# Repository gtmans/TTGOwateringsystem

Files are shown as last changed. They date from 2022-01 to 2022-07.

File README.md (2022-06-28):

##### THIS IS WORK IN PROGRESS - NOT FINISHED YET #####

  The goal of this project is to create a wireless sensoring system that controls my watering system (a rainbird raincomputer)
  Whenever one of the soilsensors signals the ground is to dry it triggers a relay that gives input to the raincomputer  

ttgo-water-DHT11

  But first I built a testing system(weatherstation). I started with these 3 modules of prox 12 euro each
  - LilyGO TTGO T-Display V1.1 ESP32 - with 1.14 inch TFT Display
  - LilyGO TTGO T-Higrow ESP32 - BME280 Sensor
  - LilyGO TTGO T-Higrow ESP32 - DHT11 Sensor (its easier to buy 2 of the same Higrows but I got stuck with these)

  I created 2 HTTP servers and one HTTP client inspired by  
  https://RandomNerdTutorials.com/esp32-client-server-wi-fi/
  https://github.com/Xinyuan-LilyGO/TTGO-LoRa-Series 
  https://gist.github.com/jenschr/0fc981415233e0751f22972811b4957f

  Wrote these 2 server programs:
  Program myESP32_server_Higrow_DHT11  Sensorserver1 IP 192.168.2.10 sleeps 70 awake 2 mins white casing
  Program myESP32_server_Higrow_BME280 Sensorserver2 IP 192.168.2.11 sleeps 70 awake 2 mins red casing
  The sensors will be placed outdoors and will be battery based so to make them power efficient 
  I let hem sleep as long as possible (the most I could realise was 70 minutes). So it wakes up every 70 minutes
  and is a server for 2 minutes then goes 2 sleep A 3D printed case can be foud on Thingiverse or Github
  
  Wrote a test program: myESP32_client_T-Display
  
  Next step was to create the base (client) station with humidity threshold setup and a relais
    
  ttgo-water-0 9display
    
  2022-01 
  Built a client based on LilyGO TTGO ESP8266 with 0.91 inch OLED Display
  Started testing:
    
  test1: 2 servers 2 min online every 70 minutes with 800Ma  lipo lasting 21 days!   
  test2: 2 servers 1 min online every 70 minutes with 800Ma  lipo lasting 32 days (2022-20-01 till 2022-21-02)
  test3: 1 servers 1 min online every 70 minutes with 1500Ma lipo lasting 40 days (2022-26-02 till 2022-06-04)
     
  2022-03 new perspective: ESPNOW
  client: LilyGO TTGO ESP8266 - with 0.91 inch OLED Display
  server: LilyGO TTGO T-Higrow ESP32 - DHT11 Sensor 
  Read about ESPNOW and did some tests. Started rewriting the code by using ESPNOW and added a lowpower client using D1 mini & capacitive soil sensor v2.0
  The lipo powered sensors in the garden will wake-up ever 70 minutes and send a message to the client and then check if message is received and goes to deepsleep.   
  If not it will wait 5 seconds and retry 3 times before going to deepsleep. With 800Ma lipo lasting prox 50 days. Sample files in ESPNOW directory
    
  2022-4 D1 mini V3.1 with capacitive soilsensor v2.0 getting 5v from LOLIN batteryshield v1.3 (every 70 minuten in deepsleep) with 800ma lipo is no success: lasts   
  only about 4 days! Going on with ESPNOW and reading things about LORA ...  
   
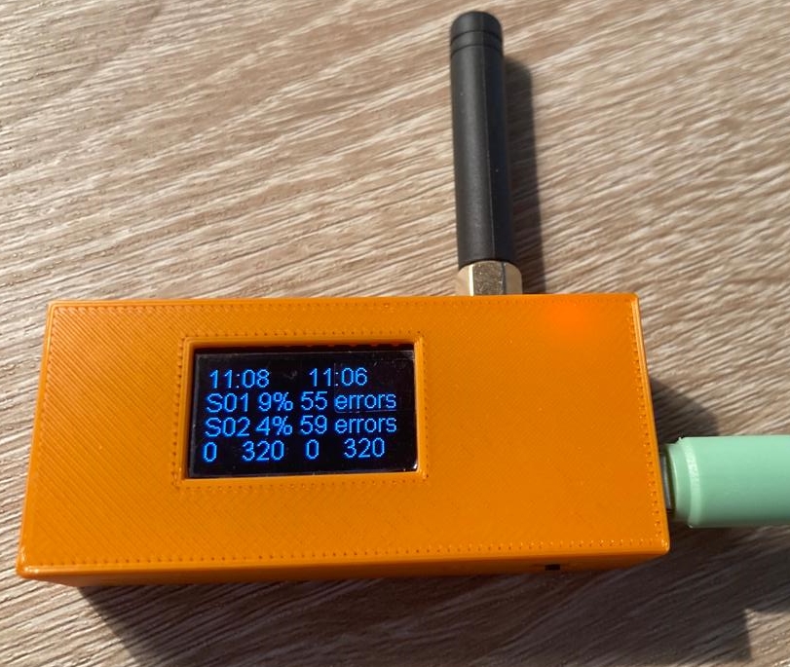
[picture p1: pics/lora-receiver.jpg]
lora-receiver
 
 
  2022-05 Started Lorawan server and client. Is working but the client stops working after some time .... 
  client: LilyGO TTGO T3 LoRa32 868MHz V2.1.6 ESP32
  server: LilyGO TTGO T-Higrow ESP32 - DHT11 Sensor with LilyGO TTGO T-Higrow LoRa Shield - 868MHz

the story continues here:
   more in the readme.md in the lorawan directory: 

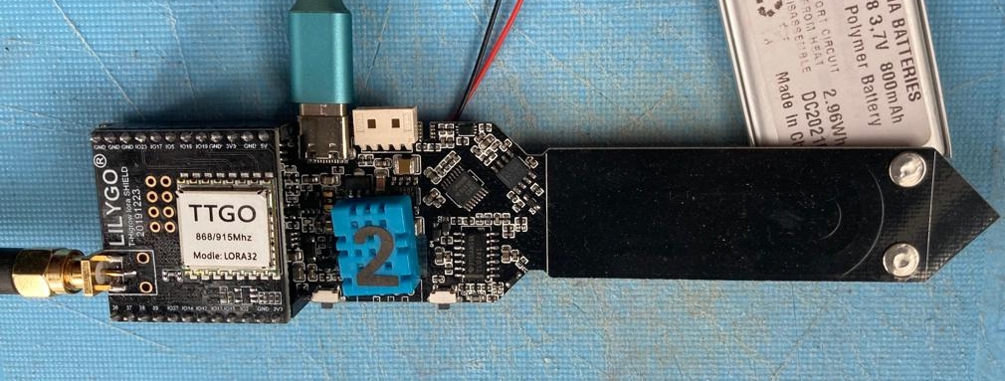
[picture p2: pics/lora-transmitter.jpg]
lora-transmitter


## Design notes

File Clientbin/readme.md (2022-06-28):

Program myESP32_client_T-Display (this program) Just 2 test things I created a sort of monster with these functions:

displays several data gained from internet such as time, weather, and the 2 servers mentioned above

displays screennumber (right above)

displays the status of the 2 sensors ** on/ofline sensr1&1

displays the health of the 2 sensors XX seen within 70 minutes

screen 1 displays internet time

screen 2 displays internet weather (temp, min temp, max temp, humidity, wind speed and direction) and minutes since last reading

screen 3 displays reading of the first sensor DHT11 (temp, humidity, soil humidity) and minutes since last reading

screen 4 displays reading of the first sensor BME280 (temp, humidity, pressure, soil humidity) and minutes since last reading

automated screen roulation

all screens have a landscape mode activated by long press right button

switch screens by short press right button

set clarity by short press left button

check server directly by long press left button

a continous measuring mode

a sleep mode option to save battery. Set go2sleep = true and sleeptime to nr. of milliseconds. After that time readings are stored to eeprom and read from eeprom when starting up

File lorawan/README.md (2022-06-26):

### PLEASE Be aware that this is an ongoing project! ####

The goal of this project is to create a wireless sensoring system that controls my watering system (a rainbird raincomputer) 
Whenever one of the soilsensors signals the ground is to dry it triggers a relay that gives input to the raincomputer

April 2022 I discovered TTGO Lorawan modules which look promising for powerconsumption and range compared to WIFI-ESPNOW.
Inspiration for this project was Timm Bogner's FDRS system:https://github.com/timmbogner/Farm-Data-Relay-System

To test and understand how it works I built a sort of LORANOW construction myself: 
The sensor modules send their readings to the client module which send a confirmation message to the sender. 
If confirmed the sender goes to deepsleep for 70 minutes (max. reliable time) In this test program time is 5 minutes.

lora-transmitter
   
The LoRaReceiver-Higrow.ino is for for (ESP32 Dev Module):LilyGO TTGO T3 LoRa32 868MHz V2.1.6 ESP32 and 
the LoRaSender-Higrow.ino   is for LilyGO TTGO T-Higrow ESP32 - DHT11 Sensor with LilyGO TTGO T-Higrow LoRa Shield - 868MHz
First power measurements of this sender setup is sleep 0,02mA/awake 40mA/lora activity 40-55mA where WIFI uses prox. 125 mA
Both are TEST programs. Finally the receiver will be added a relais and possibly a webserver. 

LORANOW construction.
All information is packet in a text string that is sent using LoRa.beginPacket();LoRa.print();LoRa.endPacket();
Because the text is readable it is simply coded:every character is replaced by another character. 
After sending the sender waits for a confirmation message by using LoRa.receive();LoRa.parsePacket();LoRa.available() and LoRa.read();

2022 may 5 status:
This setup is working perfectly with 2 sensors and 1 receiver exept for the fact that the receiver unit stops working after a few hours (12-36 sender messages)...
No clue at all where it stops - unit seems to hang but display stays on - serial monitor stops after some time (windows)

2022-05-09 Seen something interesting because the serial monitor kept on running longer as usual: The main loop keeps running while there are no more messages received (LoRa.parsePacket() does not get true). Every 60 mins it still does "resetting looptimer" as programmed. So it does not hang but stops receiving ....

2022 06-06 Problems solved. My problems were caused by: 
- testing all modules within centimeters apart from eachother
- with horizontal antennas
- with max radiopower
I made several adjustments and the test programs LoRaReceiver-higrow-16 and LoRaSender-higrow-10.7 (in workingdir) work OK and are in test
I integrated Blynk dashboard (where you can set the threshold and check all important parameters):

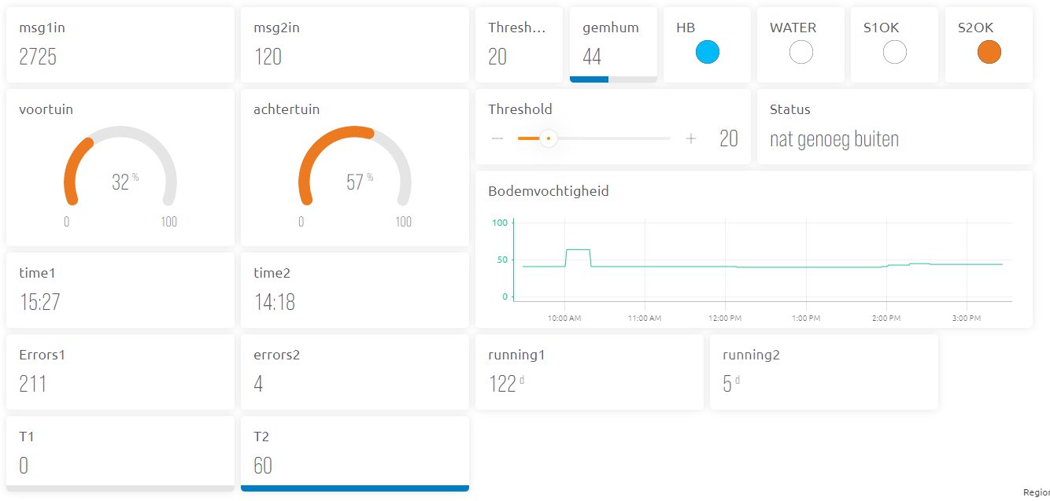
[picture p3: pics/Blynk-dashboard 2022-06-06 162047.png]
blynk_dash


2022-06-13 1st calculation of endurance is 179 days on a 800 mA lipo with sleeptime of 60 minutes (based on a test with 5 minutes sleepingtime)

2022-06-26 System up and running! (pics)

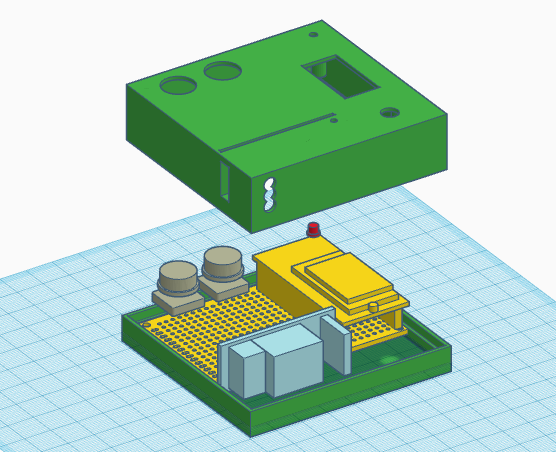
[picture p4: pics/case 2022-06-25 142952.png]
exploded

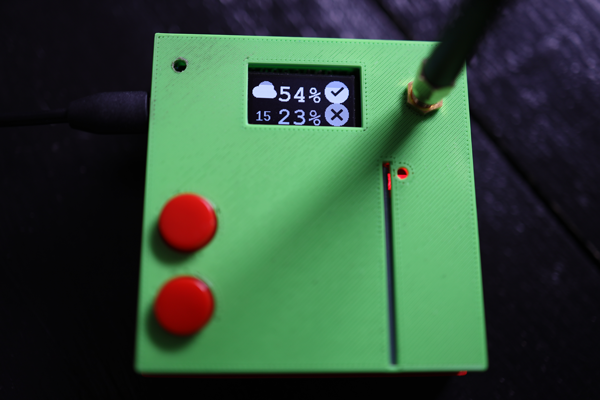
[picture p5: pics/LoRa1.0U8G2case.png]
LoRa1.0U8G2case

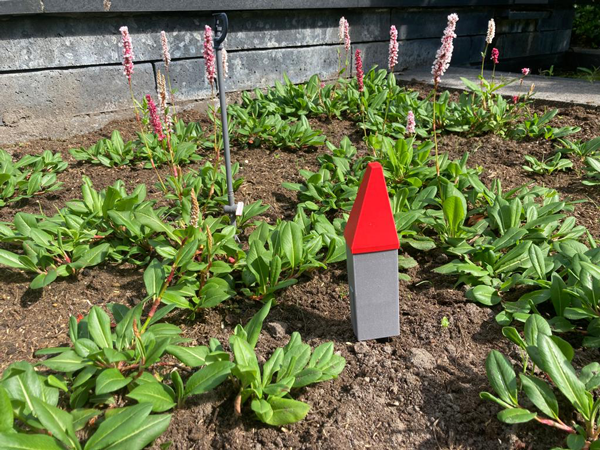
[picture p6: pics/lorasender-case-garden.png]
gardensensor


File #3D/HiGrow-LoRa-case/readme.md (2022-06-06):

All of these .stl files are my design and free to use for everybody

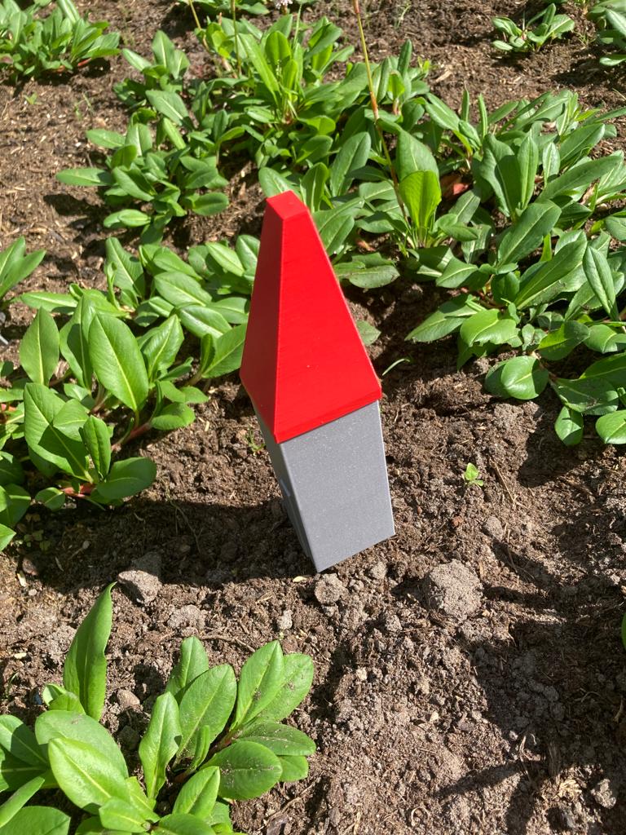
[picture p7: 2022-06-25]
pics/lorasender-case-garden2.jpg

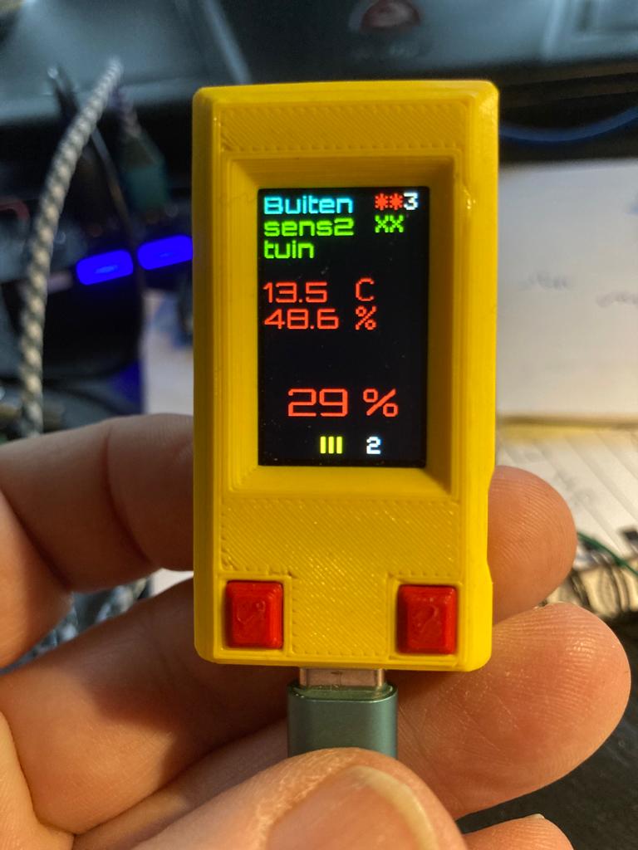
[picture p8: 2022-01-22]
pics/ttgo-water-2.jpg

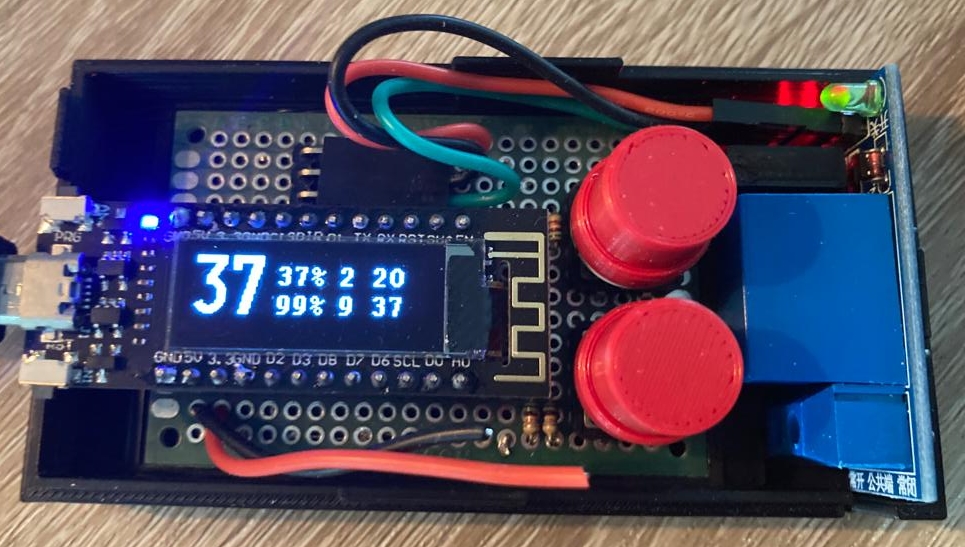
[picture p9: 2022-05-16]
pics/ESPNOW-receiver.jpg

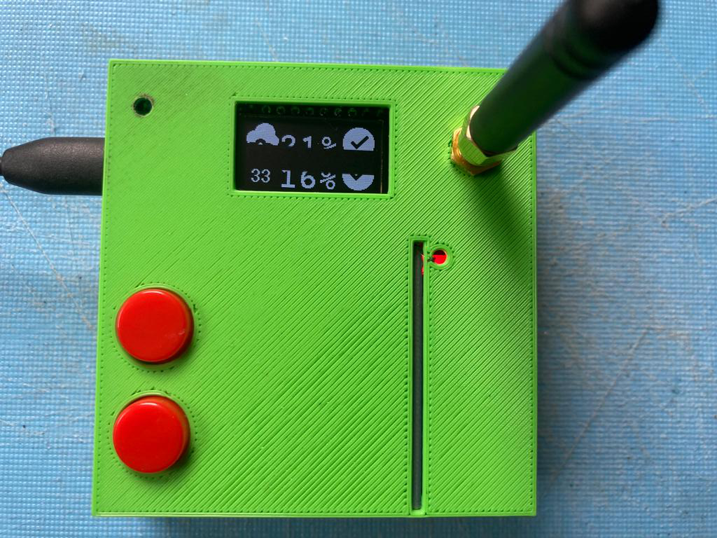
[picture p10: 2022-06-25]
pics/lorareceiver-case.jpg

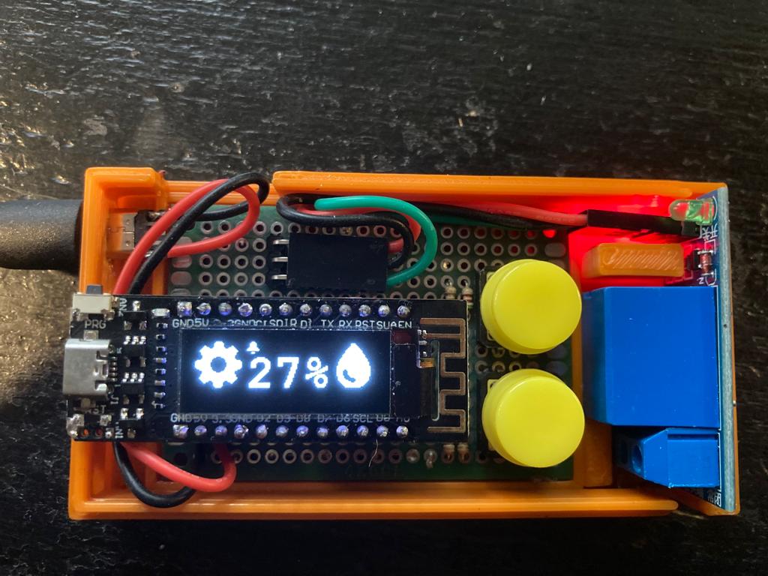
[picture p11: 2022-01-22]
pics/ttgo-water-0.9display.jpg

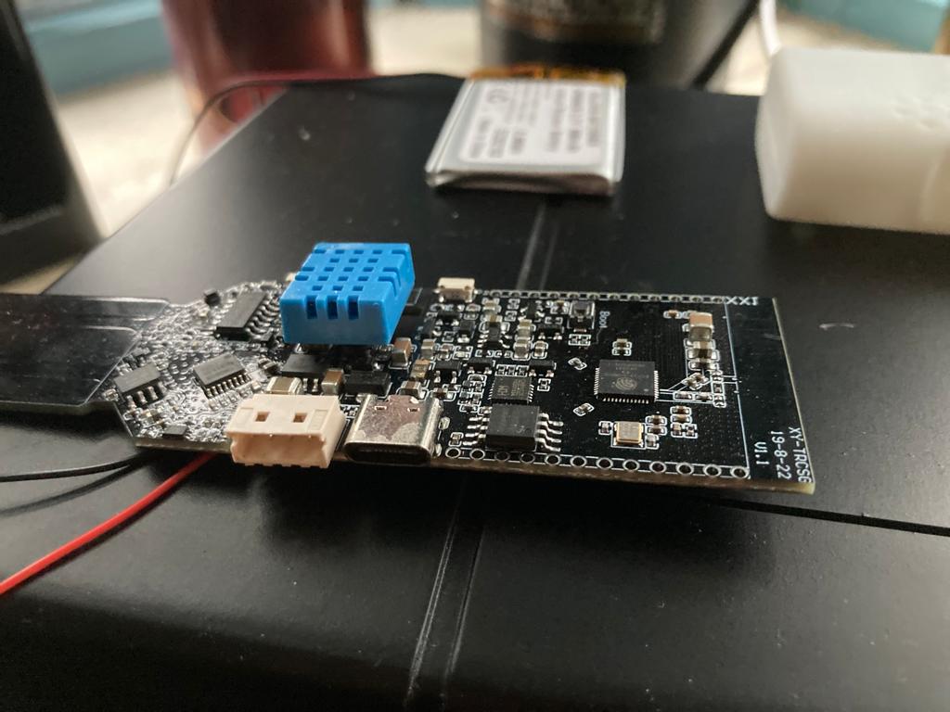
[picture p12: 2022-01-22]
pics/ttgo-water-DHT11.jpg

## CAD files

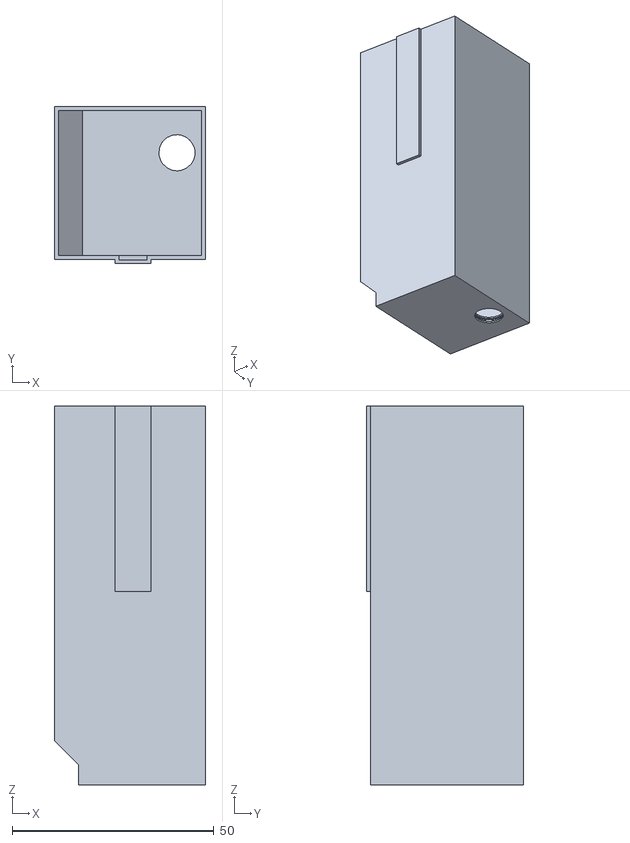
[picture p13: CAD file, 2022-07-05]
#3D/HiGrow-LoRa-case/outside case big for TTGO HIGROW LoRawan.stl
37.5 x 39.0 x 94.0

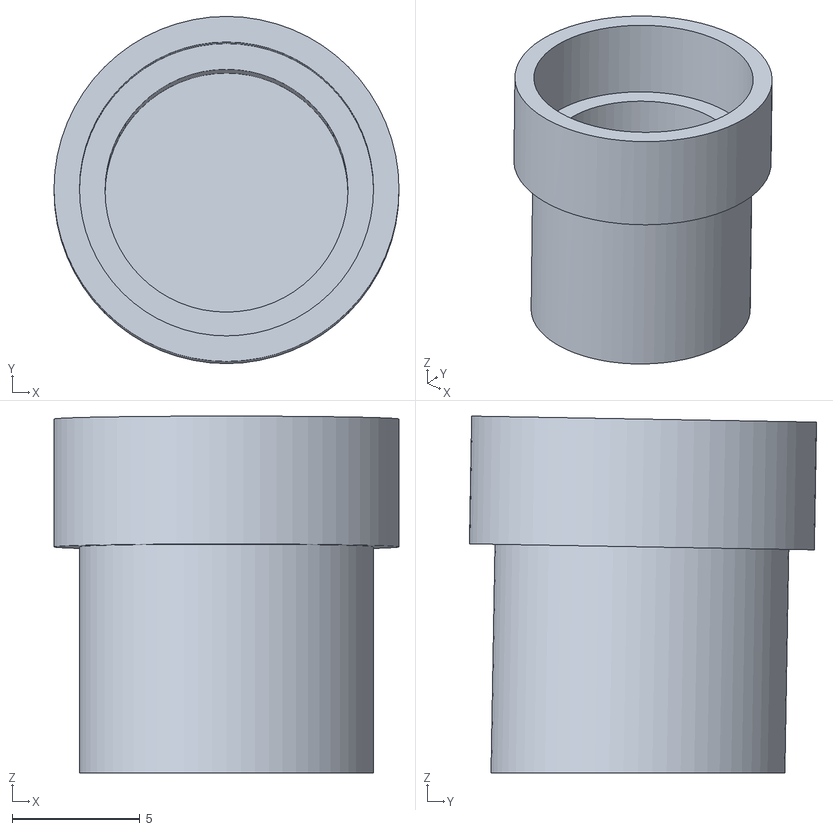
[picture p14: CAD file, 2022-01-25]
Clientbin/CASE ESP-clientv7(knob).stl
13.5 x 13.6 x 14.0

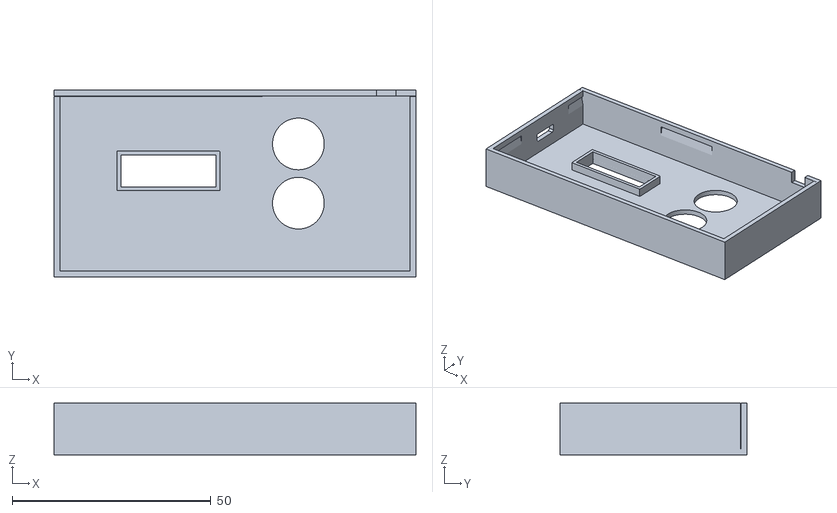
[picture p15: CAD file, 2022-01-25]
Clientbin/CASE ESP-clientv7.stl
91.1 x 47.0 x 13.0

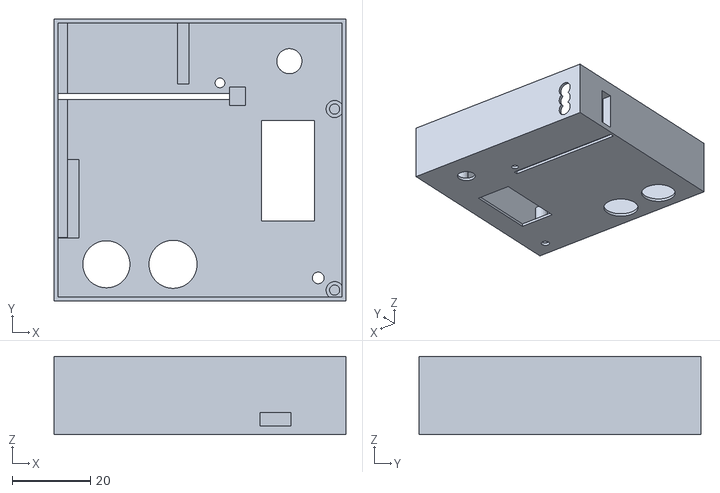
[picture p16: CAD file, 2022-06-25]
#3D/HiGrow-LoRa-case/LilyGOV4.3 TTGO LoRa32 868MHz ESP32 case.stl
74.5 x 72.0 x 20.0

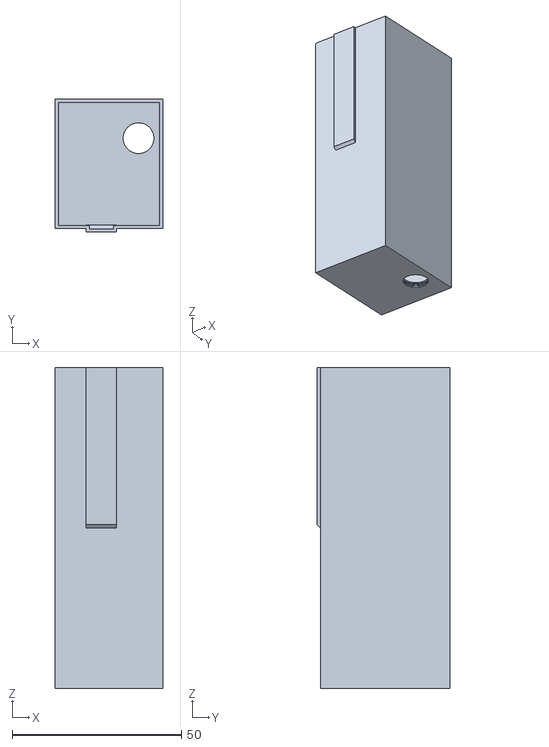
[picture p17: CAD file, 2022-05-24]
#3D/HiGrow-LoRa-case/HiGrow-LoRa-case 1.5 (5.1-101pr).stl
31.8 x 39.4 x 94.9

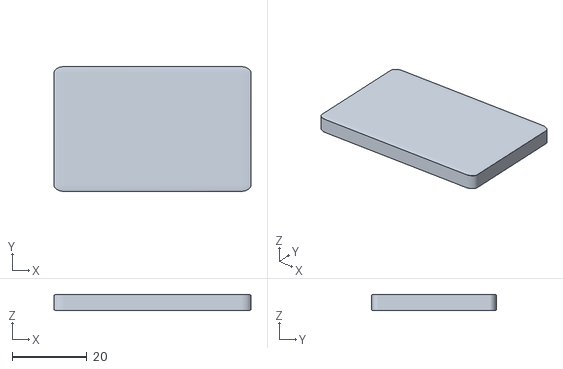
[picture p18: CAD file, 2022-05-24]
#3D/HiGrow-LoRa-case/lipo-800ma-dummy.stl
52.6 x 33.3 x 4.40

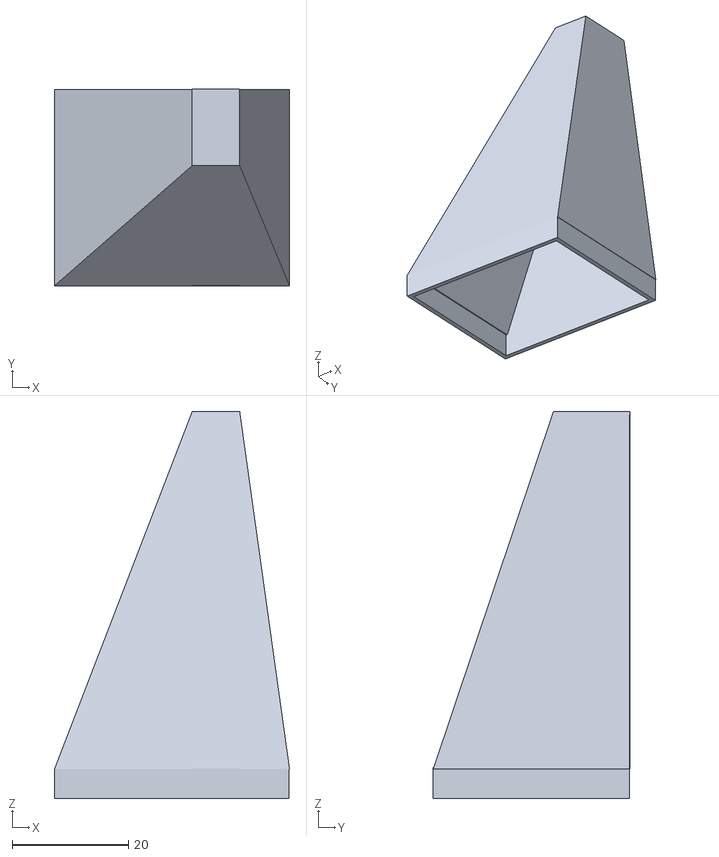
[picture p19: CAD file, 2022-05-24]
#3D/HiGrow-LoRa-case/HiGrow-LoRa-case 1.5 (6-101pr).stl
40.5 x 33.9 x 66.7

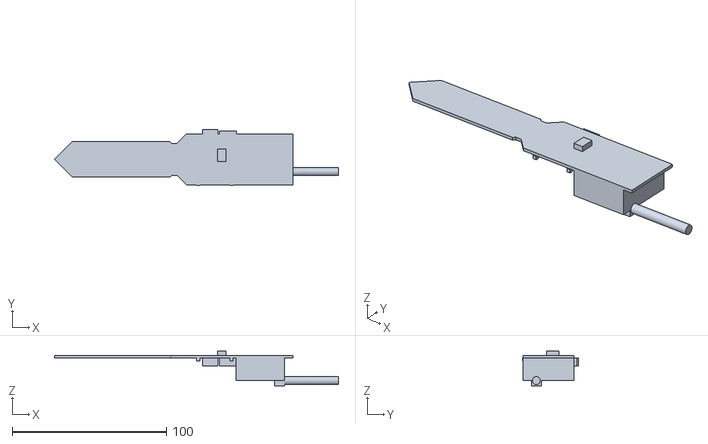
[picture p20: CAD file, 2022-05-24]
#3D/HiGrow-LoRa-case/HiGrow-LoRa-dummy.stl
183.9 x 36.5 x 22.5

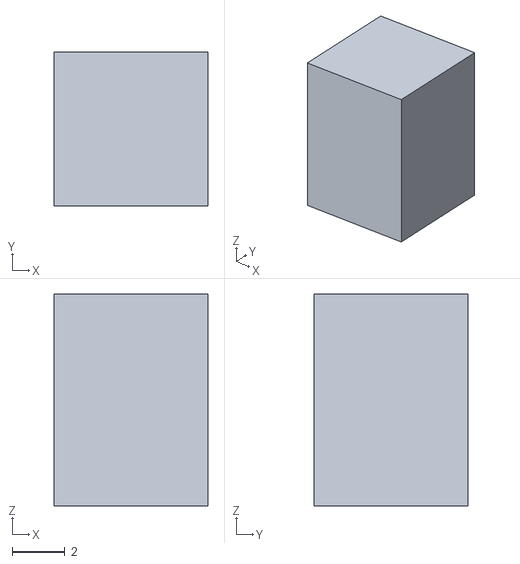
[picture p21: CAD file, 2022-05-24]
#3D/HiGrow-LoRa-case/HiGrow-LoRa-case 1.5 (4).stl
5.80 x 5.80 x 8.00

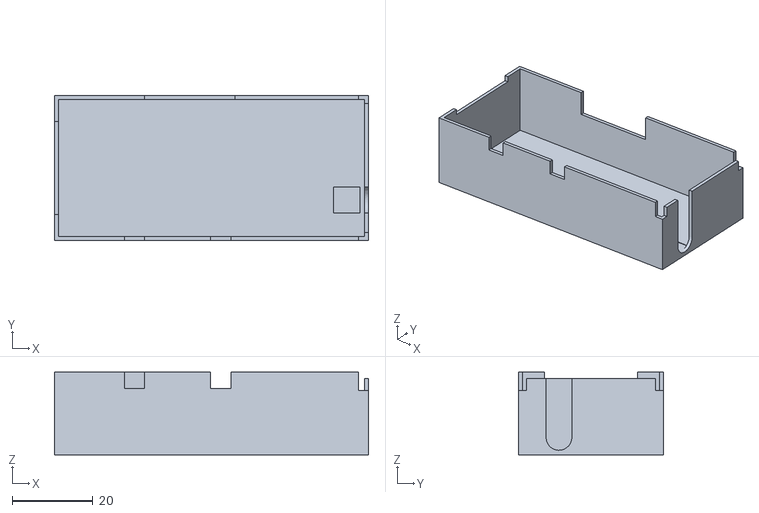
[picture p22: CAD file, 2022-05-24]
#3D/HiGrow-LoRa-case/HiGrow-LoRa-case 1.5 (1).stl
78.0 x 36.0 x 20.5

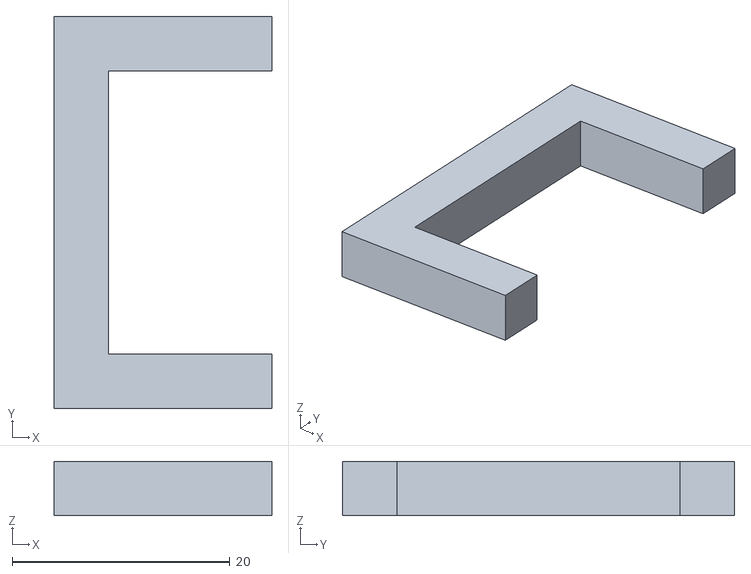
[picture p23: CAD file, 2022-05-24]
#3D/HiGrow-LoRa-case/HiGrow-LoRa-case 1.5 (3).stl
20.0 x 36.0 x 5.00

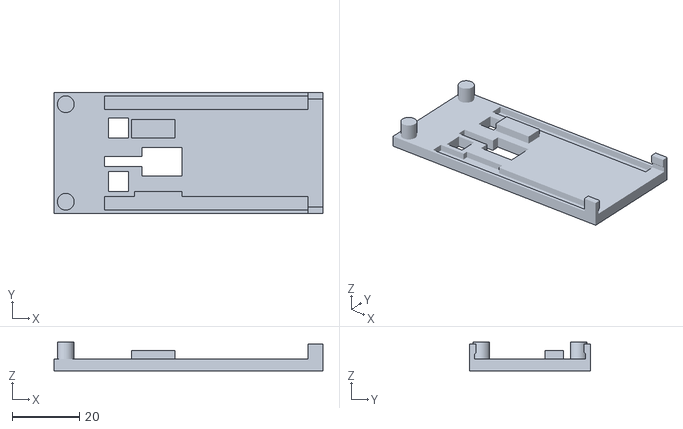
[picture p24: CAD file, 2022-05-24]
#3D/HiGrow-LoRa-case/HiGrow-LoRa-case 1.5 (2).stl
80.0 x 36.0 x 8.50

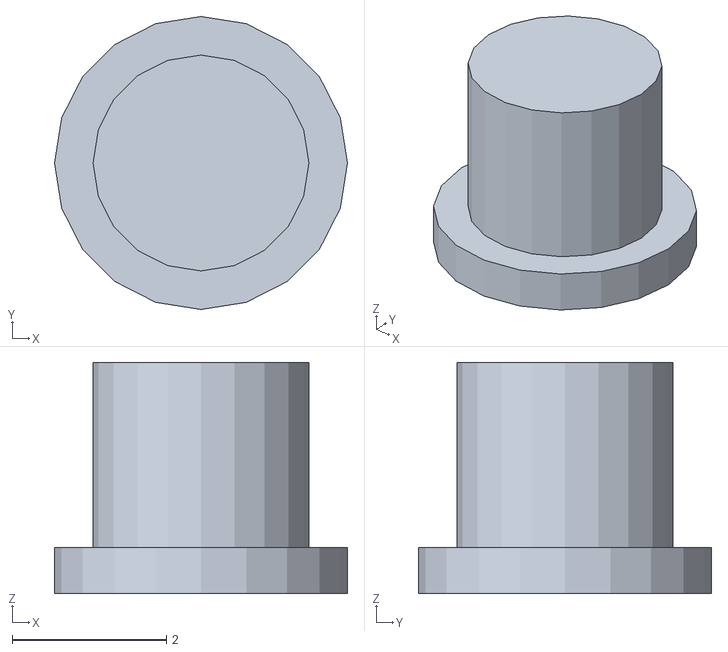
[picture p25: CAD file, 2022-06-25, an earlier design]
#3D/HiGrow-LoRa-case/LilyGOV4.3 TTGO LoRa32 868MHz ESP32 case (2).stl
3.80 x 3.80 x 3.00

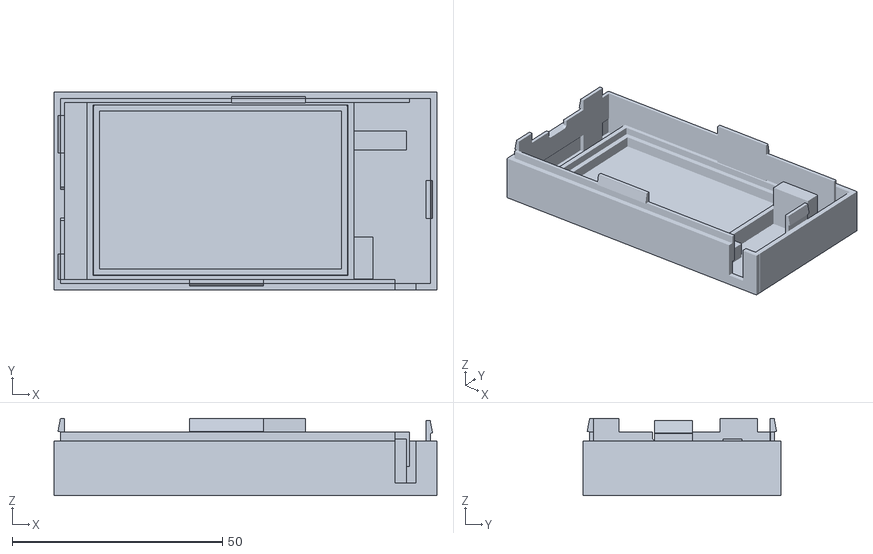
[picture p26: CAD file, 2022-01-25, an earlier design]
Clientbin/CASE ESP-clientv7 (1).stl
91.1 x 47.0 x 18.4

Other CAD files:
#3D/HiGrow-LoRa-case/LilyGOV4.3 TTGO LoRa32 868MHz ESP32 case (1).stl

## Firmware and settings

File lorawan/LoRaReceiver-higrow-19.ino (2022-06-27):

/* \Arduino\LORAWAN\TTGO-LoRa-Series-master\LoRaReceiver\LoRaReceiver-higrow-19 to use with
 * \Arduino\LORAWAN\TTGO-LoRa-Series-master\LoRaSender\LoRaSender-higrow-10.9
 * for (ESP32 Dev Module):LilyGO TTGO T3 LoRa32 868MHz V2.1.6 ESP32
 * reads text records from lorasenders higrow
 */
#define OLDLORA    1            // SET! when using 1.0 board io. 2.14
#define SND_MSG    1            // SET! confirmation message
#define USE_U8G2   1            // SET! use graphic signs io. text
#define RST_ESP    1            // SET! restart ESP every 60 min to avoid hanging(set value interval below)
#define CHK_RSSI   1            // SET! display last RSSI and SNR
#define CHK_HEAP   1            // SET! check memory heap
#define USE_WIFI   1            // SET! use WIFI to get timestamp
#define USE_EEPR   1            // SET! store la  st read values in eeprom
#define USE_BLYNK  1            // SET! use of Blynk dashboard
#define USE_RELAIS 1            // SET! version with relais and buttons
#define SND_MSGX   0            // SET! extra confirmation message
#define DEBUG      0            // SET! dump incoming string to screen or just their values
#define CHK_XTRA   0            // SET! check first byte of message is yours
#define CHK_LORA   0            // SET! check if lora.receive still active
#define USE_INSIDE 0            // SET! reduce radiosignal when testing
#define USE_SYNCW  0            // SET! use syncword to avoid stay messages (set in sender sketch too)
#define MIDNIGHT   0            // SET! restart ESP at midnight
#define NrSensors  2            // SET!
#define BUT_IN     0            // onboard button to turn screen off
#define LED_IN     2            // onboard led indicates water

#if USE_RELAIS                  // note! pinout of 1.0 and 2.0 board is different but both have these pins
  #define         relayPin  14
  #define         lbutton   12
  #define         rbutton   13 
  bool            buttons;       // are there buttons attached to set threshold? 
  bool            water   =false; 
  bool            oldwater=false; 
#endif

#if   USE_BLYNK
/*
 * https://blynk.cloud/dashboard  create a template with:
 * 
 * Id Name          Pin Datatype  Units min max def
 * 1  time1s        V0  String  
 * 2  time1s        V1  String  
 * 3  Thresholdi    V2  Integer         0   100   0
 * 4  Statuss       V3  String
 * 5  FrogardenperciV4  Integer    %    0   100   0
 * 6  BckgardenperciV5  Integer    %    0   100   0
 * 7  msg1ins1      V6  String
 * 8  msg1ins2      V7  String
 * 9  avghumi       V8  Integer         0   100   0
 * 10 wateri        V9  Integer         0   1     0
 * 11 errors1i      V10 Integer         0   32767 0
 * 12 errors2i      V11 Integer         0   32767 0
 * 13 running1i     V12 Integer    d    0   999   0
 * 14 running2i     V13 Integer    d    0   999   0
 * 15 S1OK          V14 Integer         0   1     0
 * 16 S2OK          V15 Integer         0   1     0
 * 17 Heartbeat     V16 Integer         0   1     0
 * 18 Since1i       V17 Integer         0   999   0
 * 19 Since2i       V18 Integer         0   999   0
 * 20 Thresholdseti V19 Integer         0   100   15
 * 21 RSSI1s        V20 Stringr                    
 * 22 RSSI2s        V21 Stringr                    
 * 23 Switch        V22 Integer         0   1    
 */ 
  #define BLYNK_PRINT Serial
  #if OLDLORA     // I have 2 different boards they use different template                             
    #define BLYNK_TEMPLATE_ID "TMPL878asd6f"                      // SET!
    #define BLYNK_DEVICE_NAME "mygarden"                          // SET!
    #define BLYNK_AUTH_TOKEN  "TKM9cdkslfji43566j6836j4654Wyzp8"  // SET!
  #else
    #define BLYNK_TEMPLATE_ID "TMPLklfdsj6Y"
    #define BLYNK_DEVICE_NAME "myDash"
    #define BLYNK_AUTH_TOKEN  "igpogiafgmkJHJYqwetHupoiflcdxkmU"
  #endif
  #include <BlynkSimpleEsp32.h>
  bool  flip;                     // for heartbeat led blynk
  char  auth[] = BLYNK_AUTH_TOKEN;
  int       TsinceS1;             // minutes gone since last reading sensor 1
  int       TsinceS2;             // minutes gone since last reading sensor 2
  BlynkTimer timer;
  WidgetLED led1(V9);
  WidgetLED led2(V14);
  WidgetLED led3(V15);
  WidgetLED led4(V16);
  #if !defined USE_WIFI
    #define    USE_WIFI
  #endif
#endif

#if  RST_ESP
//  long interval     = 3600000; // SET! interval  60 minutes to restart ESP every 60 min to avoid hanging
  long interval       = 7200000; // SET! interval 120 minutes to restart ESP every 60 min to avoid hanging
  long previousMillis =  millis  ();
#endif

#if  CHK_LORA
  long interval2       =  450000; // SET! interval 7.5 minutes to check lora(band) to avoid hanging
  long previousMillis2 =  millis  ();
#endif

#if  CHK_RSSI
  int snr;
  int rsi;
  int snrv [NrSensors]={0,0};
  int rsiv [NrSensors]={0,0};
#endif

#if  CHK_HEAP
  #define HEAP_DIF  10000        // SET! reset when memory loss > HEAP_DIF
#endif

#if  OLDLORA
  #include "lora1.0_board_def.h" // for 1.0  board with seperate antenna
#else  
  #include "lora2.0_board_def.h" // for 2.14 board with onboard  antenna
#endif

#if  USE_WIFI
  #include <ArduinoJson.h>
  #include <NTPClient.h>
  #include <WiFi.h>
  #include <WiFiUdp.h>
  #include <WiFiClient.h>
  #include "my_secrets.h"                       //or use 2 lines below
  //#define WIFI_SSID       "yourWIFISSID"      // ssid
  //#define WIFI_PASSWORD   "yourWIFIPassword"  // password
  //RTC
  StaticJsonDocument<1000> doc;
  WiFiUDP   ntpUDP;                // Define NTP Client to get time
  NTPClient timeClient(ntpUDP);    // Variables to save date and time
#endif

#include <SPI.h>
#include <LoRa.h>

#if USE_EEPR
  #include "EEPROM.h"
  String EepSave [NrSensors]={"11:11MYDATA01113500200020","11:11MYDATA01113500200020"};//25 long
#endif

String Sensors [NrSensors]={"S99 99% 999 errors.","S99 99% 999 errors."}; //20 long
String SensMes [NrSensors]={"?????","?????"};   //5 long
String SensTim [NrSensors]={"wait!","wait!"};   //5 long
int    NrMsgs  [NrSensors]={0,0};
int    Humi    [NrSensors]={33,33};
int    Temp    [NrSensors]={0,0};//temp or errorcounter
int    count    = 0;              // total nr of correct received packages
int    expLEN   = 20;             // SET! length of "MYDATA01102500100000"
int    flop     = 0;              // for heartbeat oled
int    mytimer  = 0;
String ID       = "MYDATA";       // SET! your chosen identifier
String expID    = ID;         
// choose your own coding/decoding strings but use same strings as in sender program
String normal   = "ABCDEFGHIJKLMNOPQRSTUVWXYZ1234567890+-";//SET! decode
String coded    = "1234567890abcdefghijklmnopqrstuvwxyz-+";//SET! code (pa A becomes 1)
String msgin    = "MYDATA01102509900000";
String msgout   = msgin;
String recv     = msgin;
String subst    = "X";
String LoRaStat = "*";
String myMessage=msgin;
String sentence=msgin;
String SN="99";                   // sensor number
String DN="9";                    // destination number
String TT="999";                  // temp reading(3)
String HH=TT;                     // hum reading (3)
String MN="99999";                // messagenumber (5)
int    T;                         // temp   reading  as integer
int    H;                         // hum    reading  as integer
int    S;                         // sensor  number as integer
int    M;                         // message number as integer
int    Threshold  = 15;
int    oldThreshold  = Threshold;
long   freememstart;  
String formattedDate="2018-05-28T16:12:34Z";
String TimeStamp="99:99";
bool   LCDon=true;
String msg;
String STHours;
String STMinutes;
int    TMinutes;
int    PrevMins[NrSensors]={0,0};
int    gemhum=15;

#if USE_U8G2
  #include <U8g2lib.h>
  // fontlists at https://github.com/olikraus/u8g2/wiki/fntlistall
  #if OLDLORA 
      U8G2_SSD1306_128X64_NONAME_F_SW_I2C u8g2(U8G2_R0, OLED_SCL, OLED_SDA , OLED_RST);
  #else
      U8G2_SSD1306_128X64_NONAME_F_SW_I2C u8g2(U8G2_R0, OLED_SCL, OLED_SDA , U8X8_PIN_NONE);
  #endif  
#else
  OLED_CLASS_OBJ display(OLED_ADDRESS, OLED_SDA, OLED_SCL);
#endif

#if  USE_BLYNK
  // This function will be called every time Slider Widget
  // in Blynk app writes values to the Virtual Pin V19
  BLYNK_WRITE(V19)
  {
  int pinValue = param.asInt(); // assigning incoming value from pin V19 to a variable
  // process received value
  Threshold = pinValue;
  Blynk.virtualWrite  (V2, Threshold);
  //Blynk.virtualWrite  (V19,Threshold);
  Serial.println    ("*blynk slider");
  }

  BLYNK_WRITE(V22)// reset switch
  {
  int pinValue = param.asInt(); // assigning incoming value from pin V19 to a variable
  // process received value
  Serial.println    ("*blynk switch");
  resettime();
  }
  
  // This function is called every time the device is connected to the Blynk.Cloud
  BLYNK_CONNECTED()
  {
      Blynk.virtualWrite  (V3 ,"Verbonden met Blynk");
      Blynk.virtualWrite  (V2, Threshold);
      Serial.println      ("Blynk_Connect");
      led1.off  ();
      led2.off  ();
      led3.off  ();
      led4.on   ();
  }
  // This function sends ESP32 uptime every 10 seconds (see timer.setInterval) to some virtual Pins
  void myTimerEvent()
  {   
//    String msg;
    gemhum =(Humi[0]+ Humi[1])/2;
    if (gemhum<Threshold){water=true;led1.on();msg="ga sproeien!"; 
    } else {water=false;led1.off();msg="nat genoeg!";}
    digitalWrite(LED_IN,water);
    if (flip){led4.on();}else{led4.off();}flip=!flip; 
    Blynk.virtualWrite  (V3,  msg);
    Blynk.virtualWrite  (V8,  gemhum);
    Blynk.virtualWrite  (V2,  Threshold);
    Blynk.virtualWrite  (V5,  Humi   [1]);
    Blynk.virtualWrite  (V4,  Humi   [0]);
  }
#endif
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
void loop(){

  unsigned long currentMillis = millis(); 
  flop++;                     //display heartbeat on oled
  if (flop>50000){            // 5   secs
    flop=0;
    if (LoRaStat=="+"){LoRaStat="x";} else {LoRaStat="+";}
    displayOled();

    #if  USE_BLYNK
    mytimer++;
    if (mytimer==10){          // prox 1 min set leds and blynk values
        mytimer=0;
        SetLeds();
      }      
    #endif 
  }

  #if USE_RELAIS  
    if (Threshold!=oldThreshold){displayThresh();ThresholdToEeprom();oldThreshold=Threshold;}
    if (water && !oldwater){        // water has become true turn on relay
      digitalWrite(relayPin,HIGH);
      oldwater=true;
      Serial.print       ("water has become true  turn on relay ");
      Serial.print       (gemhum); 
      Serial.print       ("/");
      Serial.println     (Threshold);
    }        
    if (!water && oldwater){        // water has become false turn off relay
      digitalWrite(relayPin,LOW);
      oldwater=false;    
      Serial.print       ("water has become false turn off relay ");
      Serial.print       (gemhum); 
      Serial.print       ("/");
      Serial.println     (Threshold);
    }   
  #endif
  
  #if  USE_BLYNK
    Blynk.run();
    timer.run();
  #endif
  
  #if  CHK_LORA
    if   (currentMillis - previousMillis2 > interval2) {
        if (!LoRa.begin(BAND)){
          Serial.println      ("Checking LoRa failed! Restarting ...");
          delay               (500);      
          ESP.restart         ();    
        }    
        Serial.println        ("LoRa OK, resetting looptimer");
        LoRaStat        =     "+";
        previousMillis2 =     currentMillis;
    }
  #endif

  #if  RST_ESP
    if   (currentMillis - previousMillis > interval) { 
      Serial.println        ("restarting ESP after interval.");
      delay                 (500);      
      ESP.restart           ();
    }
  #endif

  int packetSize = LoRa.parsePacket();
  if (packetSize) {  
      recv = "";
//    while (LoRa.available()) {recv += (char)LoRa.read();} ## replace
      while (LoRa.available()) {recv  = LoRa.readString();}

      #if  CHK_RSSI
        snr= LoRa.packetSnr ();
        rsi= LoRa.packetRssi();
        Serial.print        ("RSSI/SNR:");      
        Serial.print        (rsi); 
        Serial.print        ("/"); 
        Serial.println      (snr); 
      #endif
      
      int lenIN   =       recv.length();      // length of "MYDATA01100200100047"
      Serial.print        ("received package long ");      
      Serial.println      (lenIN); 

      if                  (lenIN==expLEN){
        #if CHK_XTRA
          //XTRA CHK 2 PREVENT HANGING ESP
          String CHK = recv.substring(0,1); //"c"
          int p = coded.indexOf     (CHK);  //12
          subst = normal.substring  (p,p+1);//"M"
          #if DEBUG
              Serial.print      (CHK);   
              Serial.print      (p);   
              Serial.println    (subst);           
          #endif
          if (expID.substring(0,1)!=subst){ID="X";} // extra check: 1st character of message is as expected
        #endif 
                 
        if (ID!="X"){
          codit      (recv,false);        // now convert coded msgin to msgout
          recv    =   msgout;
          ID      =   recv.substring(0,6);// "MYDATA"          
          count++;
        }
          
        if (ID==expID){
          //"MYDATA01102509900000"
          breakdown(recv);                // get vars out of message

          // now send conformation message
          // identifier send to sender 0? from receiver 1 = me received OK
          // myMessage ="MYDATA0?1OK";
        
          myMessage =expID;               //"MYDATA"
          myMessage+=SN;                  // 01 or 02
          myMessage+=DN;                  // former destination = 1 = me
          myMessage+="OK";                // "MYDATA011OK"         
          codit(myMessage,true);          // convert msgin to coded msgout
          myMessage=msgout;

          #if SND_MSG
            Serial.print        ("sending  :");   
            Serial.println      (myMessage);  
            LoRa.beginPacket    ();
            LoRa.print          (myMessage);
            LoRa.endPacket      ();
            //2testlater        LoRa.endPacket(true); // true = async / non-blocking mode
            //https://www.rfwireless-world.com/Terminology/What-is-difference-between-Implicit-header-and-Explicit-header-in-LoRaWAN-packet.html
          #else
            Serial.println      ("Not sending confirmation message.");
          #endif

          #if USE_WIFI
            formattedDate   =   timeClient.getFormattedDate();
            int pos         =   formattedDate.indexOf("T");
            TimeStamp       =   formattedDate.substring(pos+1, formattedDate.length()-1-3);
          #else
            TimeStamp       =   "99:99";
            delay (250);
          #endif

          S = SN.toInt  ();      
          ParseReadings (S,true);// store data in arrays and update counter                      
          LoRaStat  =   "R";
          
          #if DEBUG
            displayDebug();
          #else
            displayOled();          
          #endif

          #if SND_MSGX        //SEND AGAIN 2 BE SURE        
            delay             (1000); 
            Serial.print      ("sending  :");   
            Serial.println    (myMessage);  
            LoRa.beginPacket  ();
            LoRa.print        (myMessage);
            LoRa.endPacket    ();
          #else
            delay (50);
          #endif

          #if DEBUG
            displayDebug();
          #else
            displayOled();          
          #endif

          #if USE_EEPR
            WriteToEeprom       ();         // update eeprom values for reset or restart
          #endif

          #if  USE_BLYNK
              GetMinutes       (TimeStamp);
              PrevMins [S-1] = TMinutes;             
              M=SensMes[S-1].toInt();

              if (S==1){
                led2.off();
                Blynk.virtualWrite(V0 ,SensTim[0]);
                Blynk.virtualWrite(V4 ,Humi   [0]);
                Blynk.virtualWrite(V6 ,SensMes[0]);
                Blynk.virtualWrite(V10,Temp   [0]);
                Blynk.virtualWrite(V12,String(M/24));                                 //days  running 24hpd
                Blynk.virtualWrite(V20,String(snrv[0])+"/"+String(rsiv[0]));          //signal strength
              } else {
                led3.off();
                Blynk.virtualWrite(V1 ,SensTim[1]);
                Blynk.virtualWrite(V5 ,Humi   [1]);
                Blynk.virtualWrite(V7 ,SensMes[1]);
                Blynk.virtualWrite(V11,Temp   [1]);
                Blynk.virtualWrite(V13,String(M/24));                                 //days  running 24hpd
                Blynk.virtualWrite(V21,String(snrv[1])+"/"+String(rsiv[1]));          //signal strength
              }
          #endif

          #if SND_MSG
            delay(1000);LoRa.receive();                                               // after sending start receiving again
          #else
            LoRaStat="I";
            displayOled();                                                            // end of some packet same length
          #endif 
         
      } else { // not expected ID
          Serial.println  ("Package is not mine ... wrong ID ignoring package");         
      }
    } // end of len = expexted len
    else   {Serial.println("Package is not mine ... wrong length ignoring package");} // end of some packet
    
    #if CHK_HEAP //##4
      Serial.print    ("*ESP.getFreeHeap():");
      Serial.print    (ESP.getFreeHeap());
      Serial.print    (" esp_get_free_heap_size():");  
      Serial.print    (esp_get_free_heap_size());
      Serial.print    (" DIFF:");
      int freeheap = esp_get_free_heap_size()-freememstart;
      Serial.println  (freeheap);
      if              (freeheap<-HEAP_DIF){
          Serial.println          ("restarting ESP because free memory is getting low.");
          delay                   (1000);      
          ESP.restart             ();   
      } // end of small heapsize
      #endif
    }  // end of parsepacket
  #if USE_RELAIS
     checkbuttons();
  #endif
}      // end of loop

// ########################### VOIDS ###########################
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

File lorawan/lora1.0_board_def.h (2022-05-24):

#include <Arduino.h>

#define LORA_V1_0_OLED  1
#define LORA_V1_2_OLED  0
#define LORA_V1_6_OLED  0
#define LORA_V2_0_OLED  0

#define LORA_SENDER 0
// #define LORA_SENDER 1

#define LORA_PERIOD 868  
// #define LORA_PERIOD 915     
// #define LORA_PERIOD 433  

#if LORA_V1_0_OLED
#include <Wire.h> 
#include "SSD1306Wire.h" 
#define OLED_CLASS_OBJ  SSD1306Wire
#define OLED_ADDRESS    0x3C
#define OLED_SDA    4
#define OLED_SCL    15
#define OLED_RST    16
#define CONFIG_MOSI 27
#define CONFIG_MISO 19
#define CONFIG_CLK  5
#define CONFIG_NSS  18
#define CONFIG_RST  14
#define CONFIG_DIO0 26
// !    There are two versions of TTGO LoRa V1.0, 
// !    the 868 version uses the 3D WiFi antenna, and the 433 version uses the PCB antenna. 
// !    You need to change the frequency according to the board.

#define SDCARD_MOSI -1
#define SDCARD_MISO -1
#define SDCARD_SCLK -1
#define SDCARD_CS   -1

#elif LORA_V1_2_OLED
//Lora V1.2 ds3231
#include <Wire.h> 
#include "SSD1306Wire.h" 
#define OLED_CLASS_OBJ  SSD1306Wire
#define OLED_ADDRESS    0x3C
#define OLED_SDA    21
#define OLED_SCL    22
#define OLED_RST    -1
#define CONFIG_MOSI 27
#define CONFIG_MISO 19
#define CONFIG_CLK  5
#define CONFIG_NSS  18
#define CONFIG_RST  23
#define CONFIG_DIO0 26

#define SDCARD_MOSI -1
#define SDCARD_MISO -1
#define SDCARD_SCLK -1
#define SDCARD_CS   -1

#define ENABLE_DS3231

#elif LORA_V1_6_OLED
#include <Wire.h> 
#include "SSD1306Wire.h" 
#define OLED_CLASS_OBJ  SSD1306Wire
#define OLED_ADDRESS    0x3C
#define OLED_SDA    21
#define OLED_SCL    22
#define OLED_RST    -1

#define CONFIG_MOSI 27
#define CONFIG_MISO 19
#define CONFIG_CLK  5
#define CONFIG_NSS  18
#define CONFIG_RST  23
#define CONFIG_DIO0 26

#define SDCARD_MOSI 15
#define SDCARD_MISO 2
#define SDCARD_SCLK 14
#define SDCARD_CS   13

#elif LORA_V2_0_OLED
#include <Wire.h> 
#include "SSD1306Wire.h" 
#define OLED_CLASS_OBJ  SSD1306Wire
#define OLED_ADDRESS    0x3C
#define OLED_SDA    21
#define OLED_SCL    22
#define OLED_RST    -1

#define CONFIG_MOSI 27
#define CONFIG_MISO 19
#define CONFIG_CLK  5
#define CONFIG_NSS  18
#define CONFIG_RST  23
#define CONFIG_DIO0 26

#define SDCARD_MOSI 15
#define SDCARD_MISO 2
#define SDCARD_SCLK 14
#define SDCARD_CS   13

#else
#error "please select board"
#endif


#if LORA_PERIOD == 433
#define BAND 433E6
#elif LORA_PERIOD == 868
#define BAND 868E6
#elif LORA_PERIOD == 915
#define BAND 915E6
#else
#error "Please select the correct lora frequency"
#endif

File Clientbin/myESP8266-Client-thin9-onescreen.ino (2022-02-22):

/*
https://github.com/gtmans/TTGOwateringsystem 2022 by Mans Rademaker (gtmans)
for LilyGO TTGO ESP8266 with 0.91 inch OLED Display        IDE generic ESP8266
or  LilyGO TTGO T-Display V1.1 ESP32 1.14 inch TFT Display IDE ESP32   TTGO LORA32
depends on IDE setting (choice of board in IDE)
font (0.91 inch) open iconic https://github.com/olikraus/u8g2/wiki/fntgrpiconic
inspiration: http://simplestuffmatters.com/wemos-ttgo-esp8266-with-0-91-inch-oled/
inspiration: https://randomnerdtutorials.com/esp32-client-server-wi-fi/
*/
#if defined(ESP8266) //0.9 mono
  #pragma message compiling for ESP8266
  #include        <ESP8266WiFi.h>    // if ESP8266
  #include        <ESP8266Ping.h>
  #include        <ESP8266HTTPClient.h>
  #define         relayPin  1
  #define         lbutton   13
  #define         rbutton   15  
  #define         OLED_SDA  2
  #define         OLED_SCL  14
  #define         OLED_RST  4
  #include        <U8g2lib.h> 
  U8G2_SSD1306_128X32_UNIVISION_F_SW_I2C u8g2(U8G2_R0, OLED_SCL, OLED_SDA , OLED_RST);
  #define         mono 1
#elif defined(ESP32) //1.14 colordisplay
  #pragma message compiling for ESP32
  #include        <WiFi.h>           // if ESP32
  #include        <ESP32Ping.h>
  #include        <HTTPClient.h>
  #include        <TFT_eSPI.h>       // Hardware-specific library
  TFT_eSPI tft = TFT_eSPI();         // Invoke custom library
  #define         relayPin  5
  #define         portrait  0
  #define         landscape 3
  #define         lbutton   0
  #define         rbutton   35
  const int       pwmFreq           = 5000;
  const int       pwmResolution     = 8;
  const int       pwmLedChannelTFT  = 0;
  int backlight[5]                  = {10,30,60,120,220};  
#endif

#include          <Arduino.h>
#include          <SPI.h>
#include          <Wire.h>
#include          <NTPClient.h>       // https://github.com/taranais/NTPClient
#include          <WiFiUdp.h>
WiFiUDP           ntpUDP;             // Define NTP Client to get time
NTPClient         timeClient(ntpUDP); 
#include          <EEPROM.h>
#define           EEPROM_SIZE 8

int   httpResponseCode;
float avpings1  = 4;                // average #pings server1
float avpings2  = 4;                // average #pings server2
float avtime1   = 70;               // average #mins between contact server1
float avtime2   = 70;               // average #mins between contact server2
int ping1       = 0;                // #pings server1
int ping2       = 0;                // #pings server2
int oping1      = 0;                // #online pings server1
int oping2      = 0;                // #online pings server2
int totopings1  = 0;                // total of #online pings server1
int totopings2  = 0;                // total of #online pings server2
int timesinces1 = 70;               // #minutes since last seen server 1
int timesinces2 = 70;               // #minutes since last seen server 2
int OMinutes    =-1;                // total minutes since startup
int TMinutes;
int TMinutesS1;
int TMinutesS2;
int LastTMinutes= 0;
int screen      = 0;                // what screen to display
int numscreens  = 1;                // number of info screens to display -1 - extra 2 temp screens
int threshold;                      // = 25; from eeprom when dryer water!
int oldthreshold;
int humidity1   = 0;
int humidity2   = 0;
int s1online    = 0;                //times online
int s2online    = 0;
String          STHours;
String          STMinutes;
String          formattedDate;
String          dayStamp;
String          TimeStamp;
String          LastTimeStamp;
String          SoilValue[3]    =   {"","11","33"};//SoilValue[1]=reading sensor1 and SoilValue[2]=reading sensor2
const long      interval        =   15000; // check servers every 15 seconds (try 4 times a minute)
const long      interval2       =   2500;  // change display every 5 secs
unsigned long   previousMillis  =   0;
unsigned long   previousMillis2 =   0;
bool both     = false;
bool debug    = false;
bool dispping = false;
bool water    = false;        // if true:water the garden
bool oldwater = false;
bool sensor1serverup;
bool sensor2serverup;

//WIFI configuration
#include "secrets.h"
/*
// secrets.h: wifi passwords
const char* ssid     = "mySSID";        
const char* password = "myWIFIpassword";
*/
//SENSORSERVERS                 
const  IPAddress SServer1       (192,168,2,10);
const  IPAddress SServer2       (192,168,2,11);
String serverNameSoil  = "http://192.168.2.10/soilhum";
String serverName2Soil = "http://192.168.2.11/soilhum";

void setup() {
  Serial.begin      (115200);
  EEPROM.begin      (EEPROM_SIZE);
  threshold     =   EEPROM.read(0);
  if (threshold>75){threshold=35;}
  oldthreshold  =   threshold;

#if defined(mono)       //0.9 monochrome
      u8g2.begin        ();
      u8g2.setContrast(5); // x from 0 to 255 works, but do not disable oled. value x=0 still display some data..
#else
      tft.init();
      tft.setRotation   (landscape);
      tft.fillScreen    (TFT_BLACK);
      tft.setTextColor  (TFT_WHITE,TFT_BLACK);  
      tft.setTextSize   (2); 
      // set brightness
      ledcSetup         (pwmLedChannelTFT, pwmFreq, pwmResolution);//set brightness
      ledcAttachPin     (TFT_BL, pwmLedChannelTFT);
      ledcWrite         (pwmLedChannelTFT, backlight[1]);// 0-5 higher=brighter
#endif

  p1on();
  p2on();
  s1on();
  s2on();
  displaysetup();
  delay             (500);
  Serial.println    (__FILE__);//name of this doc 
  pinMode           (lbutton, INPUT);
  pinMode           (rbutton, INPUT);
  pinMode           (relayPin,OUTPUT);
  digitalWrite      (relayPin,LOW);
  setup_wifi();
  timeClient.begin(); //RTC Initialize a NTPClient to get time
  timeClient.setTimeOffset(3600);  
  whatsthetime();     //Create formatted day and timestamp
}
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
